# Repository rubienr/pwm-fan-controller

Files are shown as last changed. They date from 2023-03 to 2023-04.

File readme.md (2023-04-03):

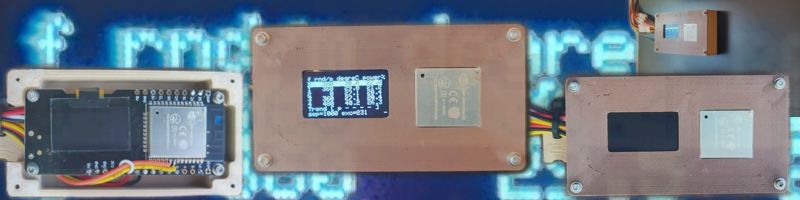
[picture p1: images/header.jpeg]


# PWM Fan Controller

A simple fan controller that controls up to 5 PWM-Fans (i.e. Nocuta 4-Pin PWM fan,
see [whitepaper](./docs/noctua_pwm_specifications_white_paper.pdf)) by monitoring
the temperature from up to 5 thermal sensors (i.e. DS18B20). The firmware monitors
temperature and generates a PWM signal for the corresponding fan.
The PWM signal is computed according to a simple pre-configured four points power curve.
The response from the fan (tacho signal) is monitored as well.

# Features

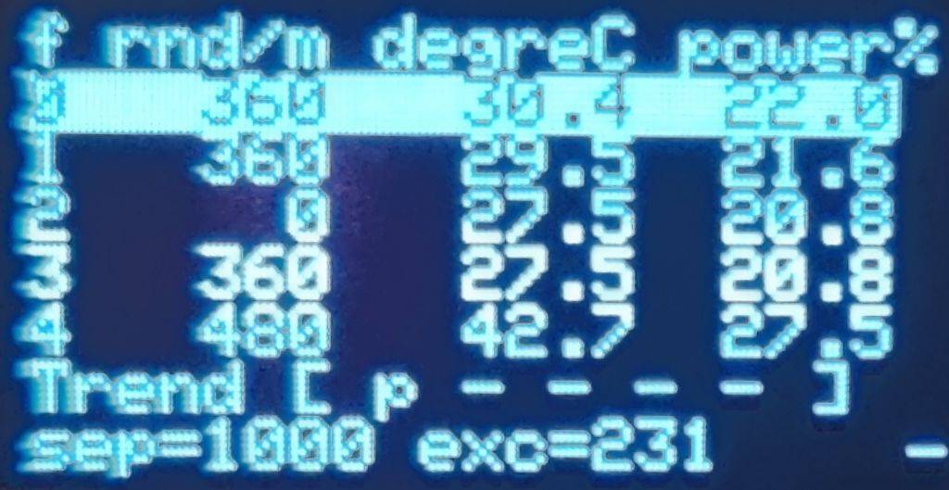
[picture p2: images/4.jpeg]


- fault detection
    - temperature sensor readout error
    - tacho signal PCNT setup error
- fault action
    - fall back to specific error-PWM
- alert if parameter exceeds configured boundary
    - temperature
    - PWM
    - RPM
- reporting
    - briefly on display
    - detailed by serial
- interactive serial console, see 'h' for supported commands
- load, modify, reset and save configuration from/to flash at runtime (serial console)
    - power curve
    - alert thresholds (RPM, PWM, temperature)
    - sensor address
    - fan reference sensor
    - logging
- OTA firmware update

# Examples

## Console commands 'h'

```bash
$ pio device monitor
h
Help:
h  print this help text:                h
f  print fan(s):                        f [fanIndex]?
L  set   auto report seconds:           L [reportSeconds]
l  print auto report seconds:           l
C  set   power curve:                   C [fanIndex] [temp0] [power0] [temp1] [power1] [temp2] [power2] [temp3] [power3]
c  print power curve(s):                c [fanIndex]?
P  set   PWM alert:                     P [fanIndex] [pwmMin] [pamMax]
p  print PWM alert(s):                  p [fanIndex]?
R  set   RPM alert:                     R [fanIndex] [rpmMin] [rpmMax]
r  print RPM alert(s):                  r [fanIndex]?
T  set   temperature alert:             T [fanIndex] [tempMin] [tempMax]
t  print temperature alert(s):          t [fanIndex]?
I  set   temperature sensor index:      I [fanIndex] [tempSensorIndex]
i  print temperature sensor(s) index:   i [fanIndex]?
A  set   temperature sensor address:    A [tempSensorIndex] [aa] [aa] [aa] [aa] [aa] [aa] [aa] [aa]
a  print temperature sensor(s) address: a [tempSensorIndex]?
S  save  settings:                      S
s  load  settings:                      s
d  print settings:                      d
x  reset settings:                      x
X  reboot device:                       X
o  enable OTA on port 3232:             o
w  print wifi settings:                 w 
W  set wifi settings:                   W "ssid" "password"
Units:
fanIndex:        uint8
tempSensorIndex: uint8
reportSeconds:   uint16, 0=disable
power[N]:        uint8
pwm[Min|Max]:    uint8
rpm[Min|Max]:    uint16
temp[Min|Max]:   int16, 1/10 Celsius (0.1C), i.e. -273.1C=-2731, 150.1C=1501
temp[N]:         int16, 1/10 Celsius (0.1C), i.e. -273.1C=-2731, 150.1C=1501, temp[N] < temp[N+1]
[aa]:            1-byte HEX address, i.e. AA, Fe, be
```

## Modify Fan Reference Sensor

```bash
# print fan to sensor dependencies
i
I 0 0
I 1 1
I 2 2
I 3 3
I 4 4
# print temperature sensors' address
a
A 0 28 FF 64 02 19 86 14 FC
A 1 28 D9 EC 09 06 00 00 F5
A 2 28 FF 64 02 19 8B D0 DE
A 3 28 64 41 0A 06 00 00 EF
A 4 28 05 52 08 06 00 00 2E
# let fan 0 depend on temperature sensor 1
I 0 1
# modify address of temperature sensor 1
A 1 28 D9 EC 09 06 00 00 FF
# save settings to flash
S
# reboot (optional)
X
```

## Boot Log

```bash
PWM controller version 0.0.2 built Fri Mar 24 00:44:03 2023
fans=5 sensors=5
Notes:
  - lines with leading '#' are human readable logs
  - lines without leading '#' are slightly machine parseable
LittleFS mounted: used=8192, total=1441792 [Bytes]
container loaded
Container:
  crc=3890207414
  Data:
    configWrites=5
    Version:
      versionNumber
        major=0
        minor=0
        patch=2
      buildTimestamp="Fri Mar 24 00:44:03 2023"
     Settings:
       serialAutoreportSeconds=0
       temperatureSensors:
         address[0]="28 FF 64 02 19 86 14 FC"
         address[1]="28 D9 EC 09 06 00 00 F5"
         address[2]="28 FF 64 02 19 8B D0 DE"
         address[3]="28 64 41 0A 06 00 00 EF"
         address[4]="28 05 52 08 06 00 00 2E"
       fans:
         fans[0]:
            defaultPwmDuty=100
            errorPwmDuty=255
            temperatureSensorIndex=0
            fanCurvePower={50, 50, 100, 100}
            fanCurveDeciCelsius={0, 250, 700, 800}
            alertBelowPwm=50
            alertAbovePwm=50
            alertBelowRpm=0
            alertAboveRpm=1500
            alertBelowTempDeciC=0
            alertAboveTempDeciC=600
         fans[1]:
            defaultPwmDuty=100
            errorPwmDuty=255
            temperatureSensorIndex=1
            fanCurvePower={50, 50, 100, 100}
            fanCurveDeciCelsius={0, 250, 700, 800}
            alertBelowPwm=1
            alertAbovePwm=254
            alertBelowRpm=0
            alertAboveRpm=1500
            alertBelowTempDeciC=0
            alertAboveTempDeciC=600
         fans[2]:
            defaultPwmDuty=100
            errorPwmDuty=255
            temperatureSensorIndex=2
            fanCurvePower={50, 50, 100, 100}
            fanCurveDeciCelsius={0, 250, 700, 800}
            alertBelowPwm=1
            alertAbovePwm=254
            alertBelowRpm=0
            alertAboveRpm=1500
            alertBelowTempDeciC=0
            alertAboveTempDeciC=600
         fans[3]:
            defaultPwmDuty=100
            errorPwmDuty=255
            temperatureSensorIndex=3
            fanCurvePower={50, 50, 100, 100}
            fanCurveDeciCelsius={0, 250, 700, 800}
            alertBelowPwm=1
            alertAbovePwm=254
            alertBelowRpm=0
            alertAboveRpm=1500
            alertBelowTempDeciC=0
            alertAboveTempDeciC=600
         fans[4]:
            defaultPwmDuty=100
            errorPwmDuty=255
            temperatureSensorIndex=4
            fanCurvePower={50, 50, 100, 100}
            fanCurveDeciCelsius={0, 250, 700, 800}
            alertBelowPwm=1
            alertAbovePwm=254
            alertBelowRpm=0
            alertAboveRpm=1500
            alertBelowTempDeciC=0
            alertAboveTempDeciC=600
       wifi:
         ssid="0xC0FFEE"
         password="*****"
 init temperature sensors ... 
 reported sensor bus power is VCC
 discovered 5 temperature sensors (index depends on bus order):
 sensorIndex=0 address=2864410A060000EF connected=true tempCelsius=24.0 resolutionBits=10
 sensorIndex=1 address=28D9EC09060000F5 connected=true tempCelsius=24.0 resolutionBits=10
 sensorIndex=2 address=280552080600002E connected=true tempCelsius=24.0 resolutionBits=10
 sensorIndex=3 address=28FF6402198614FC connected=true tempCelsius=23.9 resolutionBits=12
 sensorIndex=4 address=28FF6402198BD0DE connected=true tempCelsius=24.1 resolutionBits=12
 check configured addresses (index depends on configuration order):
 sensorIndex=0 address=28FF6402198614FC connected=true tempCelsius=23.9 resolutionBits=12
 sensorIndex=1 address=28D9EC09060000F5 connected=true tempCelsius=24.0 resolutionBits=10
 sensorIndex=2 address=28FF6402198BD0DE connected=true tempCelsius=24.1 resolutionBits=12
 sensorIndex=3 address=2864410A060000EF connected=true tempCelsius=24.0 resolutionBits=10
 sensorIndex=4 address=280552080600002E connected=true tempCelsius=24.0 resolutionBits=10
 severe input error flags: 'R'=tachoError 'T'=tempError 'S'=tempSensorError
 alert flags if parameter(s) not in range: 'p'=pwmAlert 'r'=rpmAlert 't'=tempAlert
 Enter command 'h' for help.
```

## Remote Configuring with TrueNas >13.x

Using `screen` (preferred over `cu`).
```bash
screen /dev/cuaU0 115200 # Ctrl + a then k to kill session.
```

Using `cu`. Note: when exiting `cu`, the serial state is left most likely in a "reset?" state and controller becomes unresponsive. The controller must be completeley detached and reconnected. Better use `screen`.
```bash
cu -l /dev/cuaU0 115200 # ~ then . at the beginning of line to exit session.
```

Using `stty`. Note when setting attributes with `stty`, the serial state is most left likely in a "reset?" state and controller becomes unresponsive. The contoller must be completely detached and reconnected.
```bash
cat /dev/cuaU0 # cat first then configure serial tty

stty -f /dev/cuaU0 speed 115200
echo "h" > /dev/cuaU0
```

# Wiring

Required hardware:

- One PWM channel each fan:
  - at 25kHz `ledcSetup()`, `ledcAttachPin()` and `ledcWrite()` (
    see [LEDC reference](https://docs.espressif.com/projects/esp-idf/en/latest/esp32/api-reference/peripherals/ledc.html))
  - each GPIO connected to PWM must provide pull-up
- one PCNT (Pulse Count Controller) each fan (see
  [PCNT reference](https://docs.espressif.com/projects/esp-idf/en/latest/esp32/api-reference/peripherals/pcnt.html))
- one GPIO for OneWire (software OneWire for Dallas temperature sensor bus)

Notes on ESP32:

- GPIO6 (SD_CLK), GPIO7 (SD_DATA0), GPIO8 (SD_DATA1), GPIO9 (SD_DATA2), GPIO10 (SD_DATA3), and GPIO11 (SD_CMD) are
  conntected to internal flash memory and must not be used as regular I/O.
- GPIO36-GPIO39 (SENSOR_VP, SENSOR_CAPP, SENSOR_CAPN, SENSOR_VN) can only be configured as input GPIO. These
  input-only pads do not feature an output driver or
  internal pull-up/pull-down circuitry.

Due to the required tacho-inputs and PWM-outputs for the moment only
the [lolin32 board with oled display](https://randomnerdtutorials.com/esp32-built-in-oled-ssd1306/) (ESP32) is
supported.

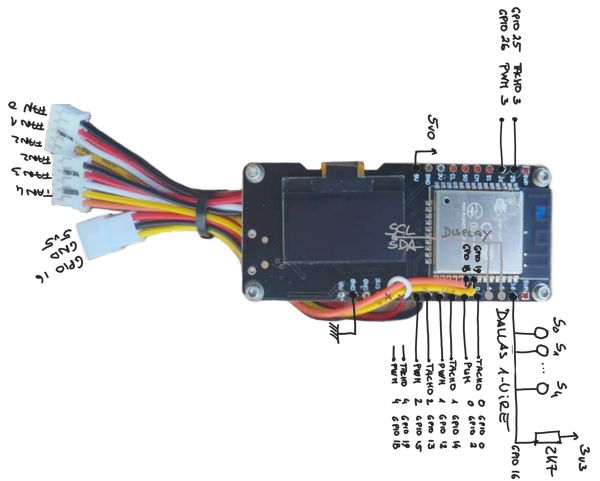
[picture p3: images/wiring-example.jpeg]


# References:

- [lolin32 board with oled display](https://randomnerdtutorials.com/esp32-built-in-oled-ssd1306/)
- [LEDC reference](https://docs.espressif.com/projects/esp-idf/en/latest/esp32/api-reference/peripherals/ledc.html)
- [PCNT reference](https://docs.espressif.com/projects/esp-idf/en/latest/esp32/api-reference/peripherals/pcnt.html)
- [Noctua whitepaper](./docs/noctua_pwm_specifications_white_paper.pdf)
- [ESP32 manual](./docs/esp32_technical_reference_manual_en.pdf)

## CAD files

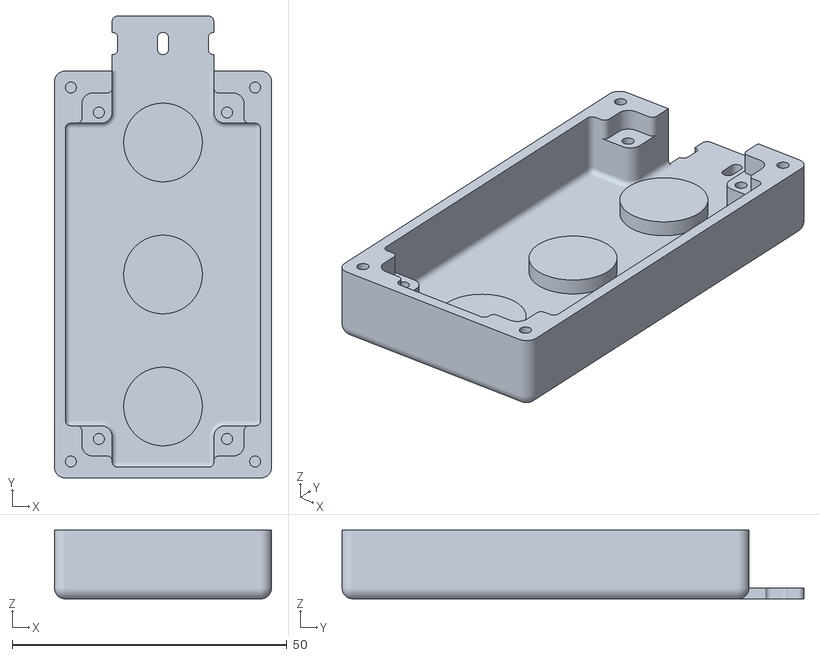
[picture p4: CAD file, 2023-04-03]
cad/case.stl
39.5 x 84.0 x 12.5

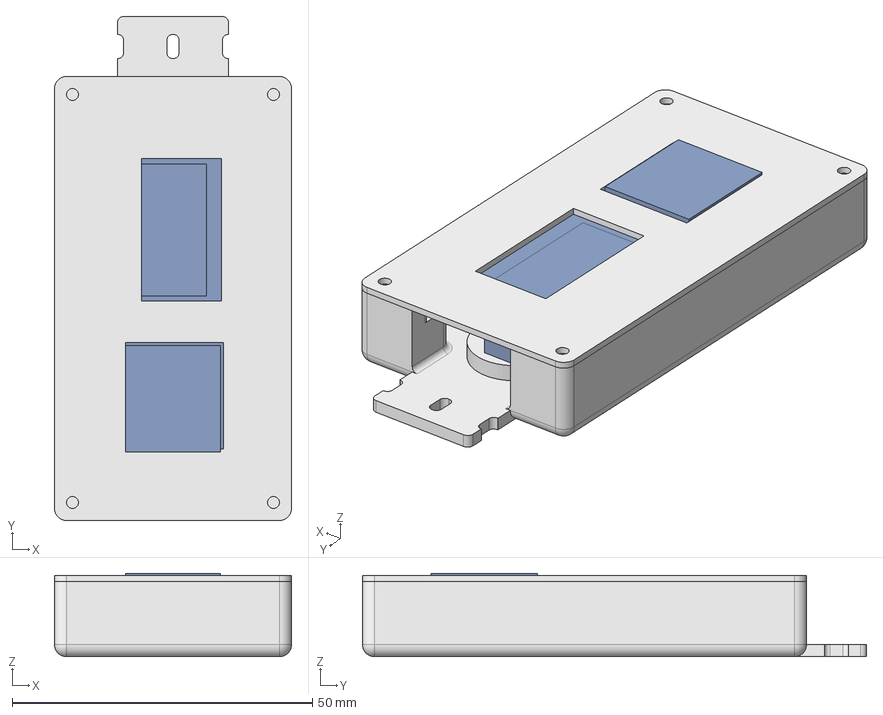
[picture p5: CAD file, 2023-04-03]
cad/lolin32-oled-clone-case.FCStd
39.5 x 84.0 x 13.9 mm
lolin32-oled-approx-model
cover
case

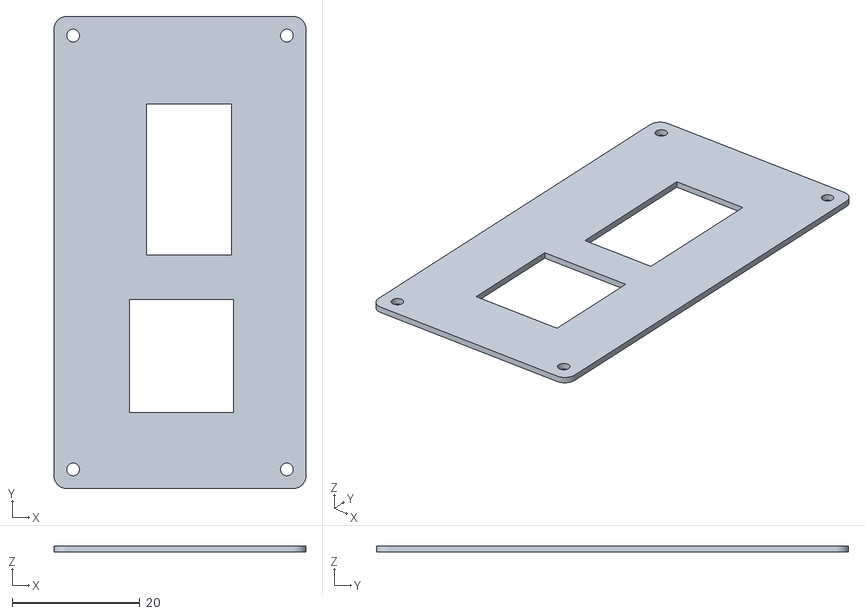
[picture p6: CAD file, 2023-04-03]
cad/cover.stl
39.5 x 74.0 x 1.00

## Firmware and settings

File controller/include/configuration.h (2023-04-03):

#pragma once
#include <cinttypes>

// ----- section: version

#define VERSION_MAJOR                 0
#define VERSION_MINOR                 0
#define VERSION_PATCH                 3

// ----- section serial

#define SERIAL_BAUD                   115200
#define SERIAL_CONFIG                 SERIAL_8N1
#define SERIAL_ECHO_ON                // echoes received characters back to serial console, comment to disable; recommended when connecting with "cu" or "screen"

// ----- section screen

#define SCREEN_WIDTH_PX               128
#define SCREEN_HEIGHT_PX              64
#define SCREEN_ADDRESS                0x3C
#define SCREEN_WIRE_SDA               5
#define SCREEN_WIRE_SCL               4

// ----- section flash settings

#define FLASH_SETTINGS_FILE_PATH_NAME "/settings.cfg"

// ----- section over the air update

#define OTA_UPDATE                    // enable feature to update firmware over wifi
#if defined(OTA_UPDATE)
    #define OTA_PORT     3232            // port number, default=3232
    #define OTA_HOSTNAME "pwmcontroller" // mdns-discoverable host name
#endif

// ----- section fans

#define FAN0 // comment to disable feature
#if defined(FAN0)
    #define FAN0_TACHO_GPIO_NUM                0                              // tacho input pin
    #define FAN0_TACHO_COUNTER_UNIT            pcnt_unit_t::PCNT_UNIT_0       // signal counter unit
    #define FAN0_TACHO_COUNTER_CHANNEL         pcnt_channel_t::PCNT_CHANNEL_0 // signal counter unit-channel

    #define FAN0_PWM_GPIO_NUM                  2     // PWM output pin
    #define FAN0_PWM_CHANNEL                   0     // PWM channel
    #define FAN0_PWM_FREQUENCY_HZ              25000 // recommended 25kHz
    #define FAN0_PWM_RESOLUTION_BITS           8     // recommended 8bit
    #define FAN0_PWM_MIN_DUTY                  0     // duty w.r.t. FANx_PWM_RESOLUTION_BITS
    #define FAN0_PWM_MAX_DUTY                  255   // duty w.r.t. FANx_PWM_RESOLUTION_BITS
    #define FAN0_PWM_DEFAULT_DUTY              100   // duty on startup w.r.t. FANx_PWM_RESOLUTION_BITS
    #define FAN0_PWM_ERROR_DUTY                255   // duty on error w.r.t. FANx_PWM_RESOLUTION_BITS

    #define FAN0_TEMP_SENSOR_INDEX             0 // temperature sensor this fan depends on
    // clang-format off
    #define FAN0_CURVE_POWER         {50,  50, 100, 100} // target power, 0-255
    #define FAN0_CURVE_DECI_CELSIUS { 0, 250, 700, 800} // input temperature; i.e. 123 corresponds to 12,34°C
// clang-format on

    #define FAN0_ALERT_BELOW_PWM               50 // trigger alert below PWM threshold w.r.t. FANx_PWM_MIN_DUTY, FANx_PWM_MAX_DUTY
    #define FAN0_ALERT_ABOVE_PWM               50 // trigger alert above PWM threshold w.r.t. FANx_PWM_MIN_DUTY, FANx_PWM_MAX_DUTY
    #define FAN0_ALERT_BELOW_RPM               0  // trigger alert below RPM threshold
    #define FAN0_ALERT_ABOVE_RPM               1500 // trigger alert above RPM threshold
    #define FAN0_ALERT_BELOW_TEMP_DECI_CELSIUS 0    // trigger alert below temperature threshold
    #define FAN0_ALERT_ABOVE_TEMP_DECI_CELSIUS 600  // trigger alert above temperature threshold

#endif

#define FAN1 // comment to disable feature
#if defined(FAN1)
    #define FAN1_TACHO_GPIO_NUM                14                             // tacho input pin
    #define FAN1_TACHO_COUNTER_UNIT            pcnt_unit_t::PCNT_UNIT_1       // signal counter unit
    #define FAN1_TACHO_COUNTER_CHANNEL         pcnt_channel_t::PCNT_CHANNEL_0 // signal counter unit-channel

    #define FAN1_PWM_GPIO_NUM                  12    // PWM output pin
    #define FAN1_PWM_CHANNEL                   1     // PWM channel
    #define FAN1_PWM_FREQUENCY_HZ              25000 // recommended 25kHz
    #define FAN1_PWM_RESOLUTION_BITS           8     // recommended 8bit
    #define FAN1_PWM_MIN_DUTY                  0     // duty w.r.t. FANx_PWM_RESOLUTION_BITS
    #define FAN1_PWM_MAX_DUTY                  255   // duty w.r.t. FANx_PWM_RESOLUTION_BITS
    #define FAN1_PWM_DEFAULT_DUTY              100   // duty on startup w.r.t. FANx_PWM_RESOLUTION_BITS
    #define FAN1_PWM_ERROR_DUTY                255   // duty on error w.r.t. FANx_PWM_RESOLUTION_BITS

    #define FAN1_TEMP_SENSOR_INDEX             1 // temperature sensor this fan depends on

    // clang-format off
    #define FAN1_CURVE_POWER         {50,  50, 100, 100} // target power, 0-255
    #define FAN1_CURVE_DECI_CELSIUS { 0, 250, 700, 800} // input temperature; i.e. 123 corresponds to 12,34°C
// clang-format on
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

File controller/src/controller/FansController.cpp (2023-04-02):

#include "FansController.h"
#include "fan/FansPwm.h"
#include "fan/FansTacho.h"
#include "fan/FansTemperature.h"
#include "sensors/TempSensors.h"
#include <cmath>


#define initFanInfo(n)                                                                                                                     \
    {                                                                                                                                      \
        fansInfo[FAN##n].interpolator.setPowerCurvePoints(FAN##n##_CURVE_POWER, FAN##n##_CURVE_DECI_CELSIUS);                              \
        fansInfo[FAN##n].pwmSpec = &fansPwm.getSpec(FAN##n);                                                                               \
        fansInfo[FAN##n].rpmSpec = &fansTacho.getSpec(FAN##n);                                                                             \
        fansInfo[FAN##n].fanTemperatureSpec = &fansTemperature.getSpec(FAN##n);                                                            \
        fansInfo[FAN##n].temperatureSensorSpec = &temperatureSensors.getSpec(fansInfo[FAN##n].fanTemperatureSpec->temperatureSensorIndex); \
    }


FansController::FansController(TempSensors &temperatureSensors, FansTemperature &fansTemperature, FansPwm &fansPwm, FansTacho &fansTacho) :
temperatureSensors(temperatureSensors), fansTemperature(fansTemperature), fansPwm(fansPwm), fansTacho(fansTacho)
{
    if(isFan0Defined) initFanInfo(0);
    if(isFan1Defined) initFanInfo(1);
    if(isFan2Defined) initFanInfo(2);
    if(isFan3Defined) initFanInfo(3);
    if(isFan4Defined) initFanInfo(4);
}


void FansController::process()
{
    temperatureSensors.requestTemperatureConversion();
    fansTacho.processEvery1000Ms();

#if defined(FAN0)
    updateFanInfo(FAN0);
#endif
#if defined(FAN1)
    updateFanInfo(FAN1);
#endif
#if defined(FAN2)
    updateFanInfo(FAN2);
#endif
#if defined(FAN3)
    updateFanInfo(FAN3);
#endif
#if defined(FAN4)
    updateFanInfo(FAN4);
#endif
}


bool FansController::hasError(uint8_t fanIndex) const
{
    return fansTemperature.getSpec(fanIndex).hasError || fansPwm.getSpec(fanIndex).hasError || fansTacho.getSpec(fanIndex).hasError;
}


bool FansController::hasAlert(uint8_t fanIndex) const
{
    return fansTemperature.getSpec(fanIndex).hasAlert() || fansPwm.getSpec(fanIndex).hasAlert() || fansTacho.getSpec(fanIndex).hasAlert();
}


void FansController::fetchTemperatureSensorData(const FanInfo &info) const
{
    const uint8_t temperatureSensorIndex{ info.fanTemperatureSpec->temperatureSensorIndex };
    temperatureSensors.fetchTemperatureCelsius(temperatureSensorIndex);
    const auto &temperatureSensorSpec{ temperatureSensors.getSpec(temperatureSensorIndex) };
    info.fanTemperatureSpec->currentTempC = temperatureSensorSpec.currentTempC;
    info.fanTemperatureSpec->hasError = temperatureSensorSpec.hasError;
}


void FansController::updateFanInfo(uint8_t fanIndex)
{
    FanInfo &info{ fansInfo[fanIndex] };
    fetchTemperatureSensorData(info);

    if(hasError(fanIndex) || forcedErrorState)
    {
        fansPwm.setErrorPwm(fanIndex);
        info.interpolatedPowerPercent = 100.0f * static_cast<float>(info.pwmSpec->errorDuty) / static_cast<float>(info.pwmSpec->maxDuty);
        info.trend = 0;
    }
    else
    {
        info.interpolator.interpolatePowerFromTemperature(info.temperatureSensorSpec->currentTempC);
        float powerRatio{ (static_cast<float>(info.interpolator.getInterpolatedPower()) / 255.0f) };
        info.interpolatedPowerPercent = powerRatio * 100.0f;
        auto newPowerPwm = static_cast<uint16_t>(roundf(powerRatio * static_cast<float>(info.pwmSpec->maxDuty)));

        if(info.pwmSpec->currentDuty == newPowerPwm) info.trend = 0;
        else if(info.pwmSpec->currentDuty > newPowerPwm) info.trend = -1;
        else info.trend = 1;
        fansPwm.setPwm(fanIndex, newPowerPwm);
    }
}

const FanInfo &FansController::getFanInfo(uint8_t fanIndex) const { return fansInfo[fanIndex]; }


FanInfo &FansController::getFanInfo(uint8_t fanIndex) { return fansInfo[fanIndex]; }

bool FansController::updateFanTemperatureSensorIndex(uint8_t fanIndex, uint8_t tempSensorIndex)
{
    if(isFanDefined(fanIndex) && isTemperatureSensorDefined(tempSensorIndex))
    {
        fansInfo[fanIndex].fanTemperatureSpec->temperatureSensorIndex = tempSensorIndex;
        fansInfo[fanIndex].temperatureSensorSpec = &temperatureSensors.getSpec(tempSensorIndex);
        return true;
    }
    return false;
}


bool FansController::updateTemperatureSensorAddress(uint8_t tempSensorIndex, const uint8_t (&address)[8])
{
    return temperatureSensors.setDeviceAddress(tempSensorIndex, address);
}

bool FansController::getTemperatureSensorAddress(uint8_t tempSensorIndex, uint8_t (&address)[8])
{
    return temperatureSensors.getDeviceAddress(tempSensorIndex, address);
}


void FansController::setForcedErrorState(bool forcedErrorFlag) { forcedErrorState = forcedErrorFlag; }

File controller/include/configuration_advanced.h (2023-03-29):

#pragma once

#include <cinttypes>

// ----- section fans

#if defined(FAN0)
    #undef FAN0
    #define FAN0 0
#endif

#if defined(FAN1)
    #undef FAN1
    #define FAN1 1
#endif

#if defined(FAN2)
    #undef FAN2
    #define FAN2 2
#endif

#if defined(FAN3)
    #undef FAN3
    #define FAN3 3
#endif

#if defined(FAN4)
    #undef FAN4
    #define FAN4 4
#endif

constexpr const bool isFan0Defined
{
#if defined(FAN0)
    true
#else
    false
#endif
};


constexpr const bool isFan1Defined
{
#if defined(FAN1)
    true
#else
    false
#endif
};


constexpr const bool isFan2Defined
{
#if defined(FAN2)
    true
#else
    false
#endif
};


constexpr const bool isFan3Defined
{
#if defined(FAN3)
    true
#else
    false
#endif
};


constexpr const bool isFan4Defined
{
#if defined(FAN4)
    true
#else
    false
#endif
};


constexpr bool isFanDefined(uint8_t fanIndex)
{
    switch(fanIndex)
    {
    case 0:
        return isFan0Defined;
    case 1:
        return isFan1Defined;
    case 2:
        return isFan2Defined;
    case 3:
        return isFan3Defined;
    case 4:
        return isFan4Defined;
    default:
        return false;
    }
}


constexpr bool hasFan0TemperatureSensorIndex(uint8_t fanTempSensorIndex)
{
    return
#if defined(FAN0)
    FAN0_TEMP_SENSOR_INDEX == fanTempSensorIndex;
#else
    false;
#endif
}


constexpr bool hasFan1TemperatureSensorIndex(uint8_t fanTempSensorIndex)
{
    return
#if defined(FAN1)
    FAN1_TEMP_SENSOR_INDEX == fanTempSensorIndex;
#else
    false;
#endif
}


constexpr bool hasFan2TemperatureSensorIndex(uint8_t fanTempSensorIndex)
{
    return
#if defined(FAN2)
    FAN2_TEMP_SENSOR_INDEX == fanTempSensorIndex;
#else
    false;
#endif
}


constexpr bool hasFan3TemperatureSensorIndex(uint8_t fanTempSensorIndex)
{
    return
#if defined(FAN3)
    FAN3_TEMP_SENSOR_INDEX == fanTempSensorIndex;
#else
    false;
#endif
}


constexpr bool hasFan4TemperatureSensorIndex(uint8_t fanTemperatureSensorIndex)
{
    return
#if defined(FAN4)
    FAN4_TEMP_SENSOR_INDEX == fanTemperatureSensorIndex;
#else
    false;
#endif
}

constexpr uint8_t maxFansCount{ 5 };


constexpr uint8_t getDefinedFansCount()
{
    uint8_t count{ 0 };
    count = (isFan0Defined) ? count + 1 : count;
    count = (isFan1Defined) ? count + 1 : count;
    count = (isFan2Defined) ? count + 1 : count;
    count = (isFan3Defined) ? count + 1 : count;
    count = (isFan4Defined) ? count + 1 : count;
    return count;
}


constexpr const uint8_t definedFanIndices[getDefinedFansCount()]
{
#if defined(FAN0)
    FAN0,
#endif
#if defined(FAN1)
    FAN1,
#endif
#if defined(FAN2)
    FAN2,
#endif
#if defined(FAN3)
    FAN3,
#endif
#if defined(FAN4)
    FAN4,
#endif
};

// ----- section temperature sensors

constexpr const bool isTemperatureSensor0Defined
{
#if defined(TEMPERATURE_SENSOR_0_ADDRESS)
    true
#else
    false
#endif
};


constexpr const bool isTemperatureSensor1Defined
{
#if defined(TEMPERATURE_SENSOR_1_ADDRESS)
    true
#else
    false
#endif
};


constexpr const bool isTemperatureSensor2Defined
{
#if defined(TEMPERATURE_SENSOR_2_ADDRESS)
    true
#else
    false
#endif
};


constexpr const bool isTemperatureSensor3Defined
{
#if defined(TEMPERATURE_SENSOR_3_ADDRESS)
    true
#else
    false
#endif
};


constexpr const bool isTemperatureSensor4Defined
{
#if defined(TEMPERATURE_SENSOR_4_ADDRESS)
    true
#else
    false
#endif
};

constexpr bool isTemperatureSensorDefined(uint8_t tempSensorIndex)
{
    switch(tempSensorIndex)
    {
    case 0:
        return isTemperatureSensor0Defined;
    case 1:
        return isTemperatureSensor1Defined;
    case 2:
        return isTemperatureSensor2Defined;
    case 3:
        return isTemperatureSensor3Defined;
    case 4:
        return isTemperatureSensor4Defined;
    default:
        return false;
    }
}

constexpr uint8_t maxTemperatureSensorsCount{ 5 };

constexpr uint8_t getDefinedTemperatureSensorsCount()
{
    uint8_t count{ 0 };
    count = (isTemperatureSensor0Defined) ? count + 1 : count;
    count = (isTemperatureSensor1Defined) ? count + 1 : count;
    count = (isTemperatureSensor2Defined) ? count + 1 : count;
    count = (isTemperatureSensor3Defined) ? count + 1 : count;
    count = (isTemperatureSensor4Defined) ? count + 1 : count;
    return count;
}


constexpr const uint8_t definedTemperatureSensorIndices[getDefinedTemperatureSensorsCount()]
{
#if defined(TEMPERATURE_SENSOR_0_ADDRESS)
    0,
#endif
#if defined(TEMPERATURE_SENSOR_1_ADDRESS)
    1,
#endif
#if defined(TEMPERATURE_SENSOR_2_ADDRESS)
    2,
#endif
#if defined(TEMPERATURE_SENSOR_3_ADDRESS)
    3,
#endif
#if defined(TEMPERATURE_SENSOR_4_ADDRESS)
    4,
#endif
};
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

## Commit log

2023-03-20 initial import
    [configuration.h]
2023-03-20 cleanup: code, logging, display; enhanced alerting; fixed PWM computation
    [configuration.h]
2023-03-21 implemented console commands
    [configuration.h]
2023-03-22 added command to change sensor address at runtime
2023-03-24 implemented flash storage: part 1
    [configuration.h]
2023-03-26 implemented flash storage: part 2
    [ConfigurationHook.h, configuration.h, configuration_advanced.h]
2023-03-26 implemented flash storage: part 3
    [ConfigurationHook.h]
2023-03-26 implemented flash storage: part 4
    [configuration.h]
2023-03-27 enabled pull-up on tacho input to save the need of external resistors
2023-03-27 updated i/o pins
    [configuration.h]
2023-03-28 enabled pcnt filter due to noise from pwm
    [FansPwm.cpp, FansTacho.cpp]
2023-03-28 enhanced pwm error handling
    [FansPwm.cpp, Firmware.cpp]
2023-03-28 fixed displayed computation of power in case of error
    [FansController.cpp]
2023-03-29 implemented FW upgrade over wifi
    [ConfigurationHook.h, configuration.h, configuration_advanced.h]
2023-04-02 disabled feature 'echo serial input'
    [configuration.h]
2023-04-02 fixed bug introduced during refactoring where fan temperature was always read from sensor 0
    [FansController.cpp]
2023-04-03 enabled "echo" per default
    [configuration.h]
2023-04-03 added documentation
    [case.stl, cover.stl, lolin32-oled-clone-case.FCStd]
2023-04-03 added example wiring illustration
